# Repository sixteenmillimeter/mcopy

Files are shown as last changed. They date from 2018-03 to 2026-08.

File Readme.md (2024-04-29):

# mcopy

An open platform for controlling small-gauge film optical printers (16mm, Super8, 8mm).

## [Project Home - git.sixteenmillimeter.com/16mm/mcopy](https://git.sixteenmillimeter.com/16mm/mcopy)

* Github Mirror - [github.com/sixteenmillimeter/mcopy](https://github.com/sixteenmillimeter/mcopy)
* Gitlab Mirror - [gitlab.com/16mm/mcopy](https://gitlab.com/16mm/mcopy)

-------
1. <a href="#intro">Introduction</a>
2. <a href="#downloads">Downloads</a>
1. <a href="#usage">Usage</a>
2. <a href="#software">Software</a>
3. <a href="#firmware">Firmware</a>
3. <a href="#hardware">Hardware</a>
4. <a href="#why">Why?</a>

-------

## Introduction 

The `mcopy` project is comprised of software and hardware for optical printers, built with re-purposed broken projectors.

#### Components

* Sequencer desktop app
* Scripting language, called `mscript`, for orchestrating complex sequences
* Arduino firmware for projectors, cameras, lights and existing printers
* 3D models of parts used for modifying projectors and printers
* Schematics for simple Arduino-based electronics
* Filmout feature for digitally transferring video and images to analog film
* Interoperability with the [intval3](https://github.com/sixteenmillimeter/intval3) intervalometer

## Downloads 

### Latest Installers

* [1.6.9](https://github.com/sixteenmillimeter/mcopy/releases/tag/1.6.9) for macOS, Linux (.deb) and Windows (.msi)

### Older Versions
* [1.6.7](https://github.com/sixteenmillimeter/mcopy/releases/tag/1.6.7) for macOS and Linux (.deb)
* [1.6.4](https://github.com/sixteenmillimeter/mcopy/releases/tag/1.6.4) for macOS, Linux (.deb) and Windows (.msi)
* [1.6.2](https://github.com/sixteenmillimeter/mcopy/releases/tag/1.6.2) for macOS
* [1.6.1](https://github.com/sixteenmillimeter/mcopy/releases/tag/1.6.1) for macOS
* [1.5.2](https://github.com/sixteenmillimeter/mcopy/releases/tag/1.5.2) for macOS
* [1.4.9](https://github.com/sixteenmillimeter/mcopy/releases/tag/1.4.9) for macOS and Linux (.deb)
* [1.2.0](https://github.com/sixteenmillimeter/mcopy/releases/tag/1.2.0) for macOS and Linux (.deb)
* [1.0.3](https://github.com/sixteenmillimeter/mcopy/releases/tag/1.0.3) for macOS and Linux (.deb)

For Windows, you can [install from source](https://github.com/sixteenmillimeter/mcopy/tree/master/app#mcopy-desktop-app) for now.

## Usage 

The software requires your hardware to be in place before the mcopy control app is useful.

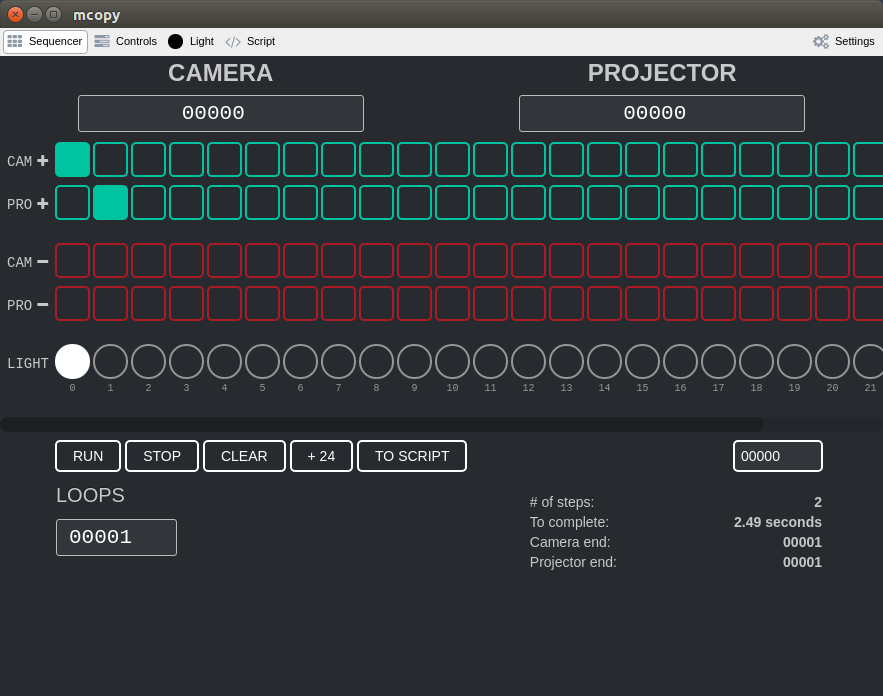
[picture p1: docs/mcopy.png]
mcopy app


## Software 

The mcopy desktop app is an Electron-based project which can be built for Linux, Windows and macOS.
Pre-built packages will be made available for macOS, initially, with the other two target platforms to follow.
To build the desktop app from source, see the [installation and running instructions](https://github.com/sixteenmillimeter/mcopy/tree/master/app#mcopy-desktop-app).
The desktop software also interoperates with two related projects; the Bluetooth + Wifi capable, Raspberry Pi-based [INTVAL3](https://github.com/sixteenmillimeter/intval3) and the Arduino-based [intval2](https://github.com/sixteenmillimeter/intval2).

## Firmware 

This project contains Arduino formware for controlling: 

* a projector
* a camera (see [intval2](https://github.com/sixteenmillimeter/intval2) for more info)
* a light
* a projector + a camera
* a projector + a light
* a camera + a light
* a camera + a projector + a light

Using a simple serial interface, this modular platform can be used to control DIY components, modified existing optical printers or a mixture of components.
The desktop app can connect to multiple serial devices, so your mcopy optical printer can be built from various designs that suit your hardware tastes/needs/available parts.

## Hardware 

All non-electronic hardware for this project is available as plaintext OpenSCAD files and 3D print-able .STL files. 
The hardware component of this project is aimed at modifying broken Bell & Howell projectors into USB serial-controlled projectors to be used in optical printing.

As a secondary capability, this desktop software and firmware package can be used to replace the sequencers for early-model JK optical printers, with some modification.

## Why? 

I'm interested in expanding the viability and access of the 16mm film format and to repurpose thre rising tide of discarded film technology.

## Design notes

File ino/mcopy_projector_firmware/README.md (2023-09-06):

# mcopy projector firmware

The goal of this firmware is to drive a JK-compatible gate
with two (2) NEMA17 stepper motors. Registration will be tracked
by four (4) IR LED emitters and receivers tracking two (2) 
double-stage rotary encoders.

1. log step index
2. calculate volate
3. analogRead() x 3
4. average readings
5. populate array with average at index

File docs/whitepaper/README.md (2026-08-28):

---
fontfamily: tgtermes
title: "mcopy: Modular Optical Tool Platform for Small Gauge Motion Picture Film"
documentclass: article
author:
- name: Matthew McWilliams
  affiliation: sixteenmillimeter.com
  email: hi@mmcwilliams.com
abstract: |
    The mcopy project consists of a modular, open-source platform for building optical tools for small gauge analog motion picture film formats.
    The platform can be used to assemble optical printers, digital transfer units and film recorders for digital images.
    Taking inspiration and guidance from free and open-source hardware and software projects, this approach aims to empower DIY projects that enable artists and artist-run film labs to build their own sytems and design their own practices around their own needs and abilities.
bibliography: sources.bib
csl: citation_style.csl
---

# Introduction

Dennis Couzin explains very plainly, in the opening line of _Notes on Optical Printer Technique_, that "an optical printer is a device for photographing the frames of one film so as to make another film." [@notes-couzin]
Consisting of a camera, a lens, a projector and a light the optical printer is a simple device that provides powerful manipulative analog capabilities to the film artist.
Optical printers allow filmmakers to control time, image and color frame-by-frame and without a digital intermediary.

The mcopy platform was started in 2009 as a one-off retrofit of a broken Bell & Howell projector.
Its initial goal was to create an optical printer with what was available at the time.
Using an Arduino, a toy DC motor, some tin foil and LEDs the first approach was made towards designing this system from otherwise discarded hardware.
Assembling this with a small copy stand and a crudely-controlled Bolex 16mm camera, it performed the function of copying film from the projector to the camera.

# Motivations

A common scenario in the analog filmmaking world is a person or organization in possession of partial or non-working optical printer.
One solution for this, potentially, would be to meticulously replace or repair any missing or non-functional parts.
This proves to be a challenge when the companies that created those parts no longer exist and the documentation for repairing these machines was either never produced or never made public.
It proves even more challenging when the individual elemental components, chips and capacitors, are no longer made in the form factors they were originally produced in and entire boards must be replaced or redesigned to support the specifications they were designed with.

Another complication to any approach to modernizing these machines is that they were produced in small batches with many changes in design between these revisions.
This makes for a very non-standard pool of components to be assembling into a single system.

A remaining solution that presents itself is to "hack" these machines and retrofit them with available techniques.
The counter to that is estabishing a common interface for this platform.
Anything that can be conformed to this new standard can be assimilated and new configurations can be built that were not possible with legacy hardware sequencers.

# Design Philosophy

Tools purpose-built for working with 16mm, Super8 and Regular 8 film are no longer regularly being produced.
There are exceptions, but without a large commercial production demand, manufacturing companies that are theoretically capable of producing the gear required to work with analog film are choosing not to.
This leaves the future of the analog cinema in the hands of its practitioners to steward the continuation and advancement of the art.
By looking to other disciplines, be they arts or sciences, artists who work with film can benefit from the ways that small-scale desktop manufacturing and rapid prototyping have both preserved and augmented other practices.

The RepRap project [@reprap-philosophy]--the "reproducible rapid-prototyper" project that kicked off a wave of open-source 3D printers--correctly does not spend any time focusing on producing alternatives for "cheap and ubiquitous parts like screws and electric motors".
If there is an existing, standard and available part that solves a problem, it saves time and effort inclding it.
Those resources are better spent focusing on the core requirements of the project which, in this case, is to make a cheap and accessible contact printer for artists.

The RepRap project is not a perfect foundation on which to base the entirety of the design of this contact printer, however.
The conclusion drawn by Adrian Bower--an engineer, not a philosopher or historian--that Marxism provides a correct diagnosis of Capital but it's solution is the "all-time worst-idea in human history" [@reprap-philosophy] is both ahistorical and works against the entire purpose of the project.
Contact printing, as a means of film production, benefits more people by shifting from a mode limited to a class of professional film lab operators to a more accessible capability available to artists and artist-run film labs who operate at a sub-industrial scale.

The Arduino project [@arduino-about] created an explosion of capabilities that are now available to hobbyists and educators by making an open and extendable platform of programmable microcontrollers.
Amateurs are offered the ability to control physical electronic hardware with code in a way that was completely inaccessible due to cost and complexity only years prior.
The Arduino improved on the Parallax BASIC Stamp, a closed-source physical computing platform that required special software for the build toolchain, replacing it with an open-source board and an integrated development environment (IDE) for easily programming the board that could run cross-platform. [@arduino-os]
By leveraging the tools themselves--Arduino microcontrollers and software--as well as the projects' own approach to making an open, clear and accessible way to work with electronics the mcopy project can prioritize simplicity and openness over complexity and trade secrets held for profit.

What emerges from the synthesis of newly-accessible machine-computer interfaces and open manufacturing technologies is the possibility to create new tools that serve the needs filmmakers have today.
Every component can be represented by a serial device that connects to a computer and those devices can be sequenced and controlled by a common application.

By pursuing modular design, filmmakers can use the mcopy platform to create multi-purpose tools that change their functionality by changing their configuration.
Making an mcopy-controlled camera module for a film-to-film optical printer saves the time and effort of creating a second mcopy-controlled camera module for a film out digital recording system; they can be the exact same camera with only a different image source.
Similarly the system can be used to swap a film camera for a digital one; the sequencer neither cares nor needs to know whether it's controlling a Bolex or a DSLR.
It just has to operate them in the correct order without overlapping.

Two already emergent advantages over closed-source alternatives are the clear and simple plaintext protocol and the sequencer application that runs cross-platform and ties the system together.

# Serial Protocol

At the heart of the functionality of intermittant-motion film printers like an optical printer is the sequencing of discrete actions.
If the camera and projector both run at the same time, or if one is moving before the other completes an action, motion blur will be introduced to the images.
Frames of film must be resting in place for rephotographing onto film or "scanning" the image digitally in these systems.
So, as a result, the mcopy serial protocol has a simple but effective rule: all physical actions are done one-at-a-time and with request and then confirmation steps.
If the camera is triggered to capture a frame with a byte `c` then the camera device must return that byte `c` to confirm that it is complete and is not moving.

There is a library of action command bytes, an ever-growing list, but at the time of this writing represent a mostly-complete range of functionality for a variety of modular hardware components.

Devices, as of now, are expected to operate on `57600` baud and be excessible over serial by any capable serial client.

# Desktop Application

Due to the simplicity of the protocol, the mcopy desktop application existed in many forms before settling as a cross-platform Electron [@electron] app.

The earliest version was a PHP web application that would compile a sequence into a byte array and then send that over serial to the, then, single Arduino that controlled the physical hardware.
The immediate drawback here is that PHP executes per-request, meaning that the serial connection would have to be re-initalized each time there's a user-interaction or a more complicated logic that would keep a device persisted would need to be put into place.
I had neither the capability or inclination to make this work.

The next version was built in Processing [@processing]--a Java-based application that was built for creative programming--which was much more appropriate for the task but has other drawbacks.
The general-purpose graphical interfaces for Processing, things like text inputs and forms, are not ideal and were difficult to develop with and use.

# Retrofitting Existing Hardware

# New Hardware

Retrofitting existing hardware was always intended as the first step to producing new hardware modules that could eventually completely replace all legacy machine parts.
This approach is sometimes referred to as a "Ship of Theseus pattern" [@wiki-shipoftheseus] and in this application is, simply put: build machines using parts that people and organizations already have until total replacements can be designed.
The practice of retrofitting hardware, in this case, requires the kind of inspection that makes designing replacements possible: detailed measurements, documenting electrical diagrams, and review of sourced components.
Two examples of this pattern being applied and materializing new modular components are the projector and gate designs.

## The Projector

## The Gate

## References

---
refs: |
   ::: {#refs}
   :::
...

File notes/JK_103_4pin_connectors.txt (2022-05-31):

# Ebay

Vintage Cinch Jones 4 Pin Male Connector
https://www.ebay.com/itm/133497068900

VINTAGE CINCH JONES 4 PIN Male Connector Plug
https://www.ebay.com/itm/133633184716

Pair Cinch Jones 4-pin Female Connector Mountable Socket Angle Bracket NOS (QTY)
https://www.ebay.com/itm/224122802125

CINCH P-304-CCT POWER PLUGT 4 PIN
https://www.ebay.com/itm/154258653116

Cinch Jones Beau Molex P-304-cct 38331-5604 Power Connector Plug 4 Pin
https://www.ebay.com/p/20039272321

Beau Cinch S304CCT Jones 4 Pin Socket 38331-8004 Connector Cable Clamp Top
https://www.ebay.com/itm/133503417945

CINCH JONES BEAU MOLEX S-3304-CCT-L 38331-8204 SOCKET 4PIN w/ LATCH FOR YAESU
https://www.ebay.com/itm/400445955283

# NEW

https://www.newark.com/cinch-connectivity-solutions/p-304-cct/plug-socket-connector-plug-4-position/dp/39F282

https://www.alliedelec.com/product/cinch/p304hcct/70152797

brass, stainless steel, brass coated steel

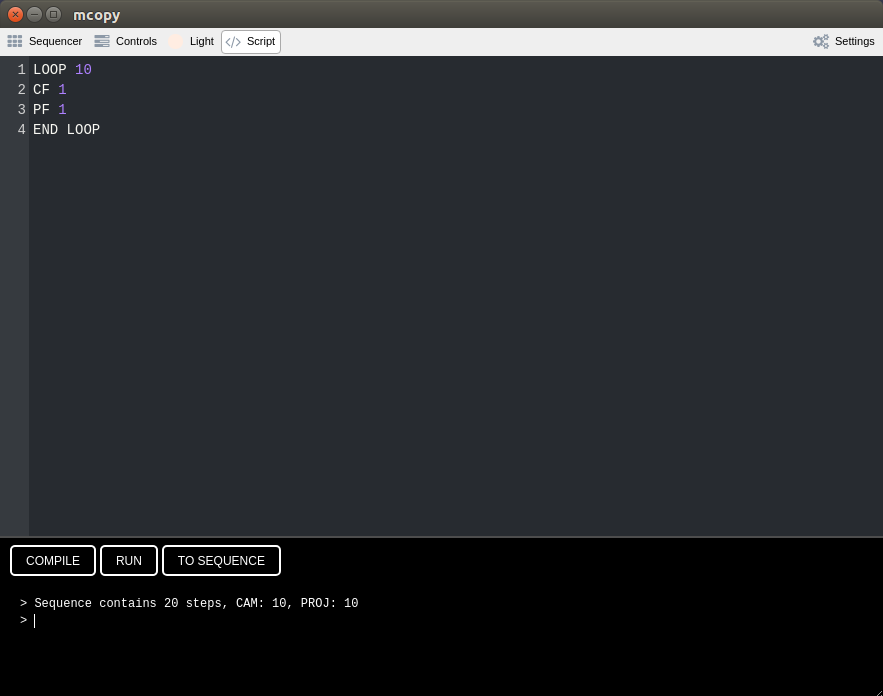
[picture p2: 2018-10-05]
docs/mcopy4.png

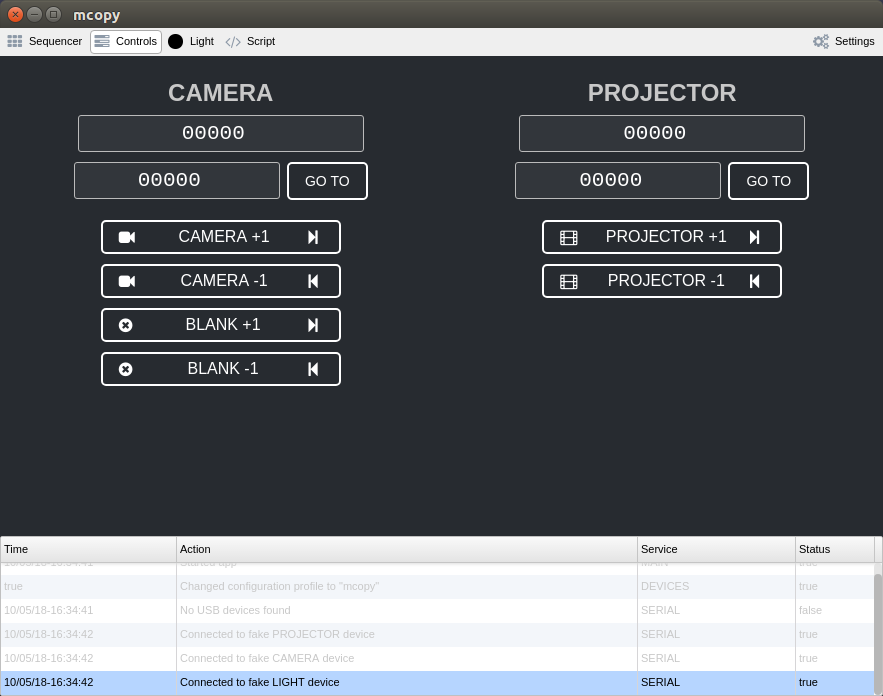
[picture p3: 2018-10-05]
docs/mcopy2.png

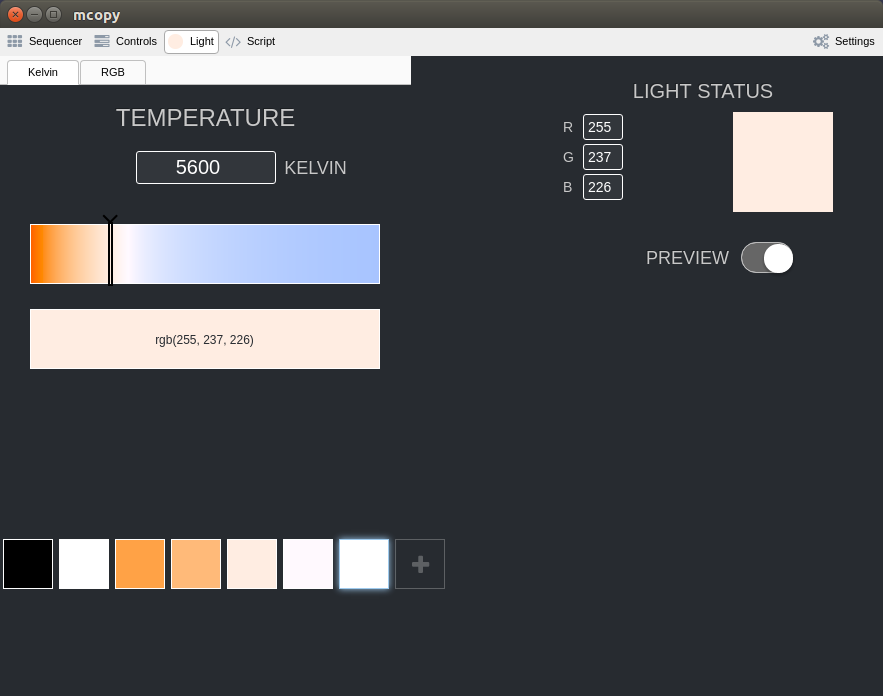
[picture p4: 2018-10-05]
docs/mcopy3.png

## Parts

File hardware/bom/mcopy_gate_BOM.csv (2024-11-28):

module | quantity | part | part_id | description
front_block_pegs | 2 | M2.5 hex cap bolt 10mm | N/A | Fasctens front_block_pegs to front_block
front_block | 4 | M2.5 hex nut | N/A | Attach the film path blocks
front_block | 2 | M5 hex cap bolt 25mm | N/A | Attach the front_block to the body
body | 2 | 608-RS Ball Bearing | 608-RS | Center sprocketed_roller in gate voids and allow for smooth rotation
body | 2 | M3 hex nut | N/A | Attach slide_catch to gate
body | 12 | M2.5 hex nut | ISO 4032 | Attach idle_roller and filter_holder and slide_rail to gate
body | 4 | M2.5 hex cap bolt 10mm | N/A | Attach slide_rail to gate
body | 2 | M2.5 hex cap bolt 25mm | N/A | Attach filter_holder to gate
body | 6 | M2.5 hex cap bolt 16mm | N/A | Attach idle_roller to gate
body | 2 | M5 hex nut | N/A | Attach front_block to gate
body | 2 | M5 hex cap bolt 20mm | N/A | Attach gate to projector
sprocketed_roller_nut_16mm | 2 | M2.5 hex nut | ISO 4032 | Attaches the bolt to the nut
sprocketed_roller_nut_16mm | 2 | M2.5 hex cap bolt 16mm | ISO 4762 | Attaches the nut to the sprocketed roller
back_plate | 1 | M2.5 hex cap bolt 10mm | N/A | Join the front_plate to the back_plate
front_plate | 1 | M2.5 hex nut | ISO 4032 | Join the front_plate to the back_plate

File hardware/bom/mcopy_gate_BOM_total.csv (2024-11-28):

quantity | part | part_id | price
2 | M5 hex nut | N/A | 10
2 | M5 hex cap bolt 25mm | N/A | 54
2 | M5 hex cap bolt 20mm | N/A | 38
2 | M3 hex nut | N/A | 7
19 | M2.5 hex nut | N/A | 120
2 | M2.5 hex cap bolt 25mm | N/A | 12
8 | M2.5 hex cap bolt 16mm | N/A | 112
7 | M2.5 hex cap bolt 10mm | N/A | 98
2 | 608-RS Ball Bearing | 608-RS | 36
46 | TOTAL | N/A | 487

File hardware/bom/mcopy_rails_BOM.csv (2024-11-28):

module | quantity | part | part_id | description
sled | 8 | 608-RS Ball Bearing | 608-RS | To smooth sled moving along rails
sled | 2 | Linear bearing | N/A | For center rails
sled | 2 | T8 Nut | Tr8x2 | For drive screw

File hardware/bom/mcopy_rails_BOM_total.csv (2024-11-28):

quantity | part | part_id | price
2 | T8 Nut | Tr8x2 | 499
2 | Linear bearing | N/A | 200
8 | 608-RS Ball Bearing | 608-RS | 143
12 | TOTAL | N/A | 842

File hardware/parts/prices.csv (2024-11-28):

part | part_id | price | quantity | url
M3 hex nut | N/A | 999 | 300 | https://amzn.to/4hAnwjc
M2.5 hex nut | ISO 4032 | 629 | 100 | https://amzn.to/4i7qxrr
M2.5 hex cap bolt 10mm | N/A | 699 | 50 | https://amzn.to/49froT4
M2.5 hex cap bolt 16mm | N/A | 699 | 50 | https://amzn.to/49cj6v2
M2.5 hex cap bolt 25mm | N/A | 598 | 100 | https://amzn.to/41faYb0
M3 hex cap bolt 6mm | N/A | 726 | 100 | https://amzn.to/3AwiZxo
M3 hex cap bolt 8mm | N/A | 899 | 100 | https://amzn.to/3YEvWNB
M3 hex cap bolt 12mm | N/A | 836 | 100 | https://amzn.to/48CGa5Y
M3 sliding t slot nut | N/A | 599 | 105 | https://amzn.to/48GRrSU
M5 hex cap bolt 20mm | N/A | 949 | 50 | https://amzn.to/4ePHCmW
M5 hex cap bolt 25mm | N/A | 809 | 30 | https://amzn.to/3VgdQAW
M5 hex nut | N/A | 999 | 200 | https://amzn.to/3ZdMNHs
2020 Aluminum extrusion mm | N/A | 7399 | 12200 | https://amzn.to/418OicC
100RPM DC geared motor with encoder | N/A | 1619 | 1 | https://amzn.to/3UF707G
250RPM DC geared motor | JSX40-370 | 1499 | 1 | https://amzn.to/3NWkcRL
ESP32 Dev board | N/A | 1999 | 3 | https://amzn.to/3NXCvGj
L298N Motor driver module | N/A | 1149 | 4 | https://amzn.to/4ellssy
ESP32 GPIO breakout board | N/A | 1199 | 2 | https://amzn.to/3UFjpbO
M4 hex bolt 40mm | N/A | 609 | 10 | https://amzn.to/4ikpYL8
608-RS Ball Bearing | 608-RS | 1779 | 100 | https://amzn.to/4fKxDA7
Linear bearing | LM8UU | 1199 | 12 | https://amzn.to/4i5XsMZ
T8 Nut | Tr8x2 | 499 | 2 | https://amzn.to/3B4m4VW

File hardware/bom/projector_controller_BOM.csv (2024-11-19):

module | quantity | part | part_id | description
electronics_attachment | 2 | M3 hex cap bolt 12mm | N/A | Attach to electronics mount
electronics_mount | 2 | M3 hex nut | N/A | Attach electronics attachment
electronics_mount | 4 | M3 hex cap bolt 8mm | N/A | Attach Arduino Uno

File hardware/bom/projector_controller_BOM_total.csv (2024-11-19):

quantity | part_id | part | price
2 | M3 hex nut | N/A | 6
4 | M3 hex cap bolt 8mm | N/A | 0
2 | M3 hex cap bolt 12mm | N/A | 18
8 | N/A | TOTALS | 24

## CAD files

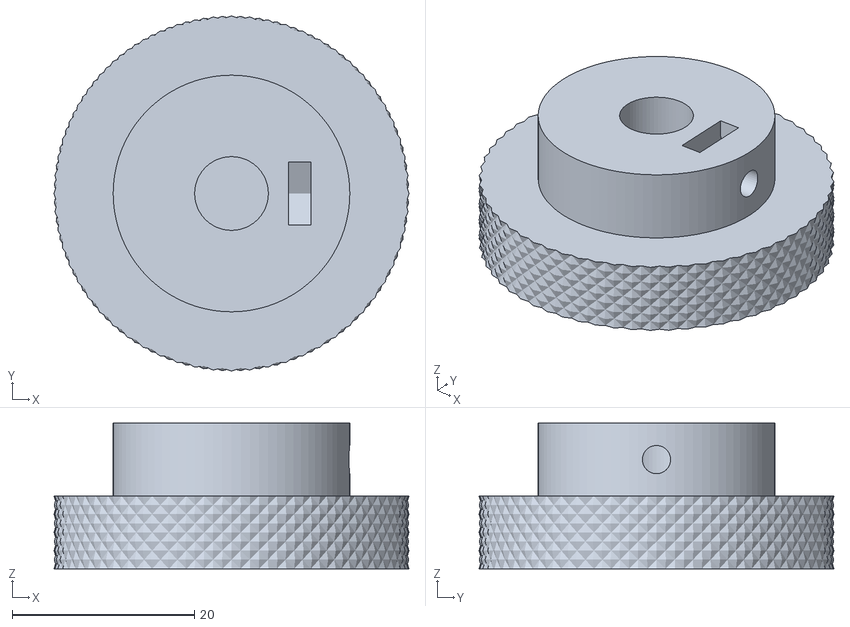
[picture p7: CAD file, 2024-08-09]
stl/mcopy_lens_assembly_threaded_knob.stl
39.0 x 39.0 x 16.0

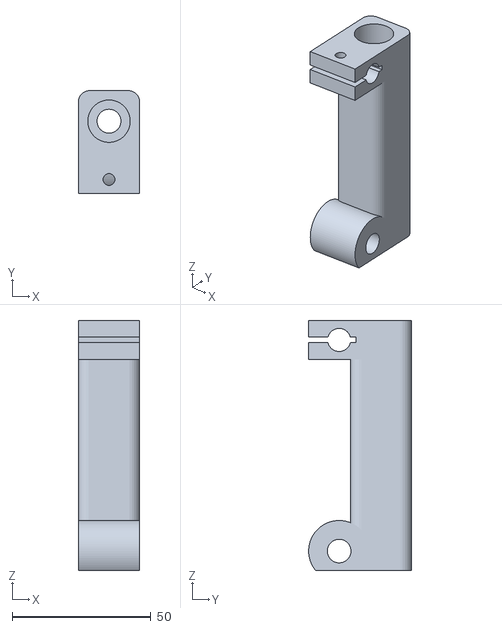
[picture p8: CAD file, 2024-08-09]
stl/mcopy_lens_assembly_linear_z.stl
22.0 x 37.0 x 90.0

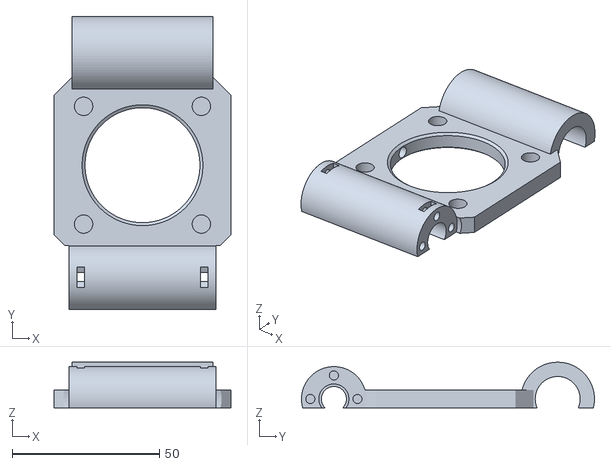
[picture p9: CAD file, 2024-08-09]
stl/mcopy_lens_assembly_bellows_board_magnetic.stl
60.0 x 99.5 x 15.5

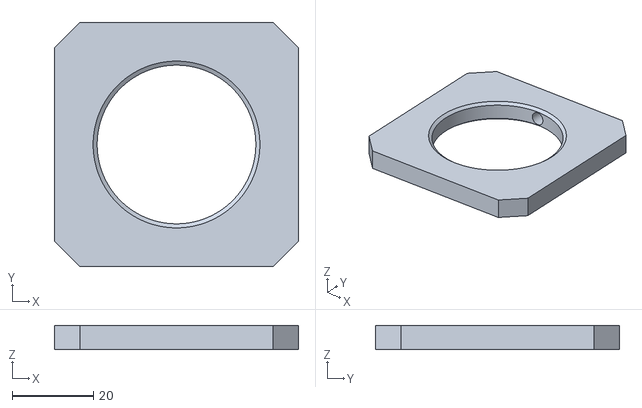
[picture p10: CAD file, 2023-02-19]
stl/jk_lens_assembly_camera_bellows_board.stl
60.0 x 60.0 x 6.00

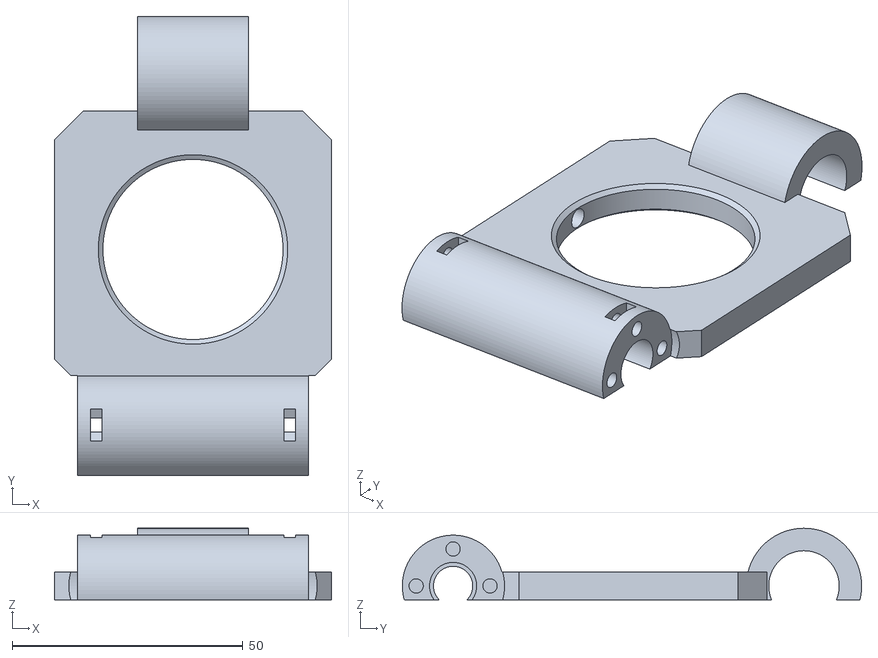
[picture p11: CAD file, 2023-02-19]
stl/jk_lens_assembly_bellows_board.stl
60.0 x 99.5 x 15.5

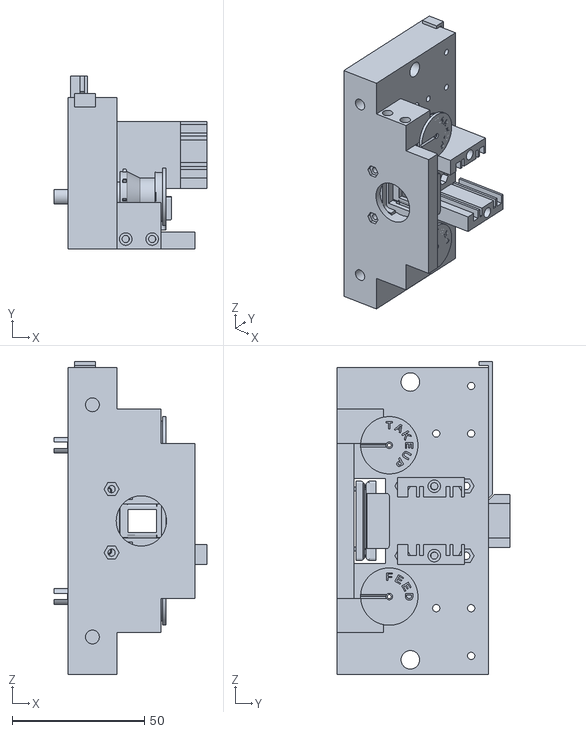
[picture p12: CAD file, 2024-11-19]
debug/mcopy_gate.stl
57.7 x 65.4 x 118.3

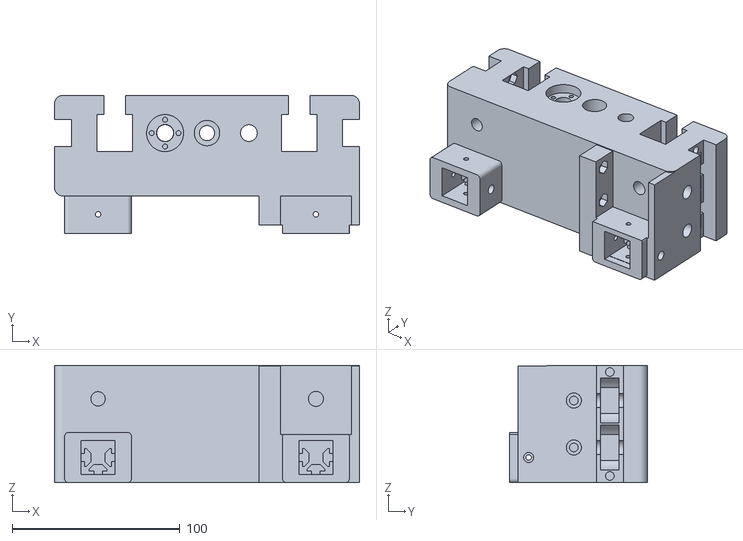
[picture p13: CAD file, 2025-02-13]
stl/mcopy_rails_lens_sled.stl
182.0 x 82.5 x 70.0

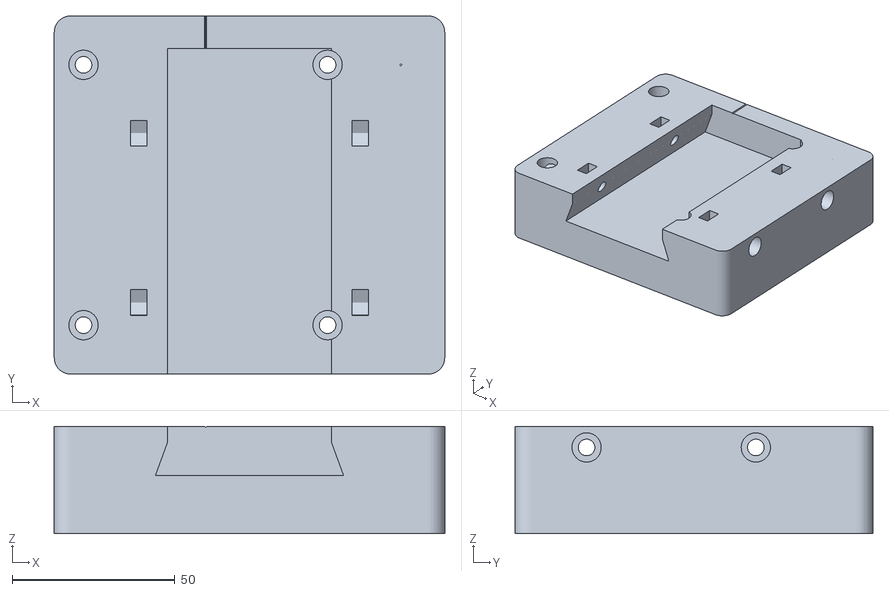
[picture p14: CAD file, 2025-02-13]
stl/mcopy_rails_camera_sled_bolex.stl
120.0 x 110.0 x 33.0

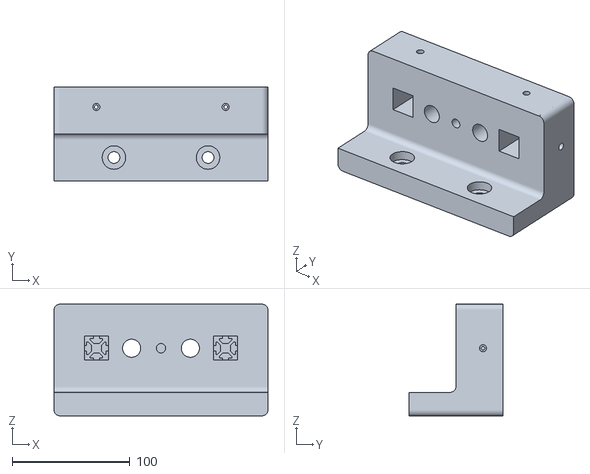
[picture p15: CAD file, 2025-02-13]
stl/mcopy_rails_rail_end_idle.stl
182.0 x 80.0 x 95.0

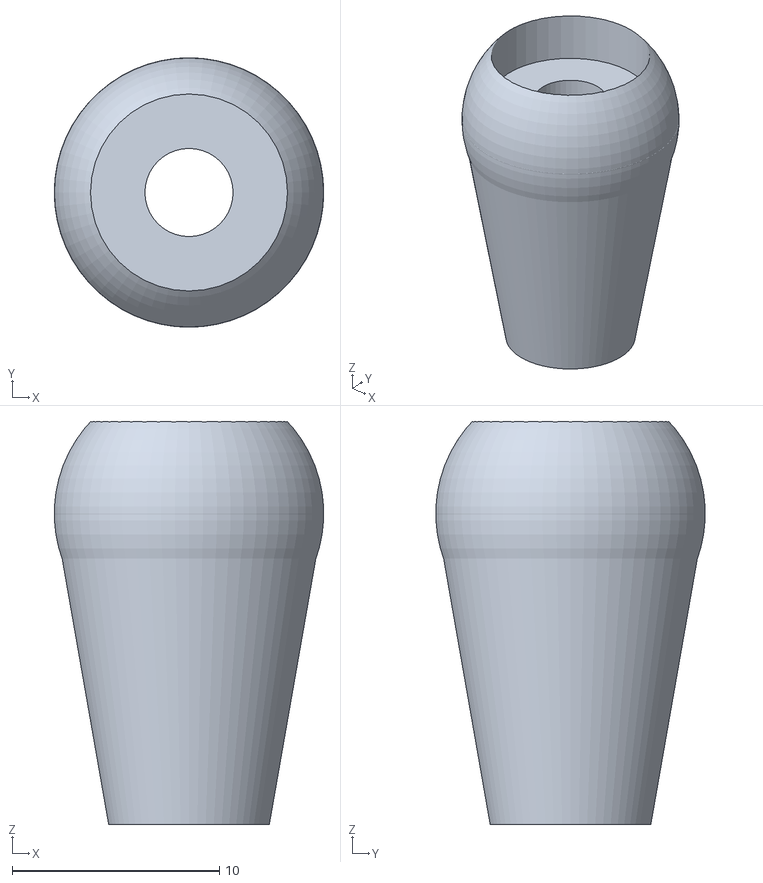
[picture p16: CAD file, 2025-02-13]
stl/mcopy_rails_dial_handle.stl
13.0 x 13.0 x 19.4

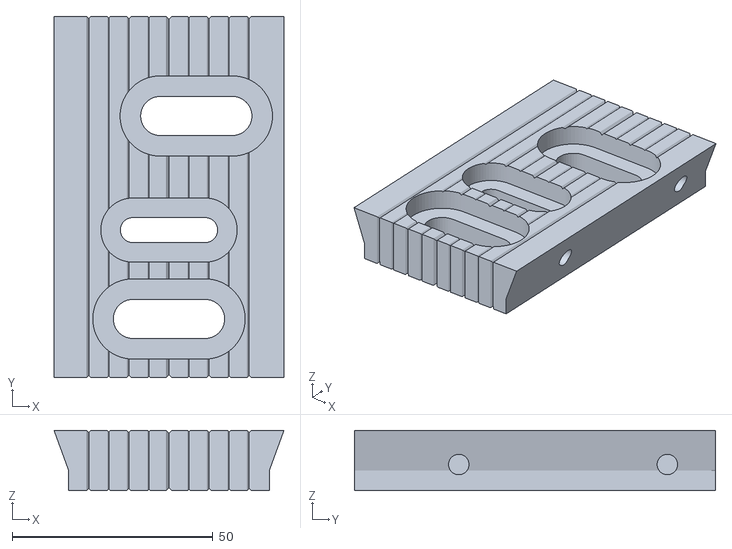
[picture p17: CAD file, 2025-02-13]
stl/mcopy_rails_camera_sled_bolex_plate.stl
57.3 x 90.0 x 15.0

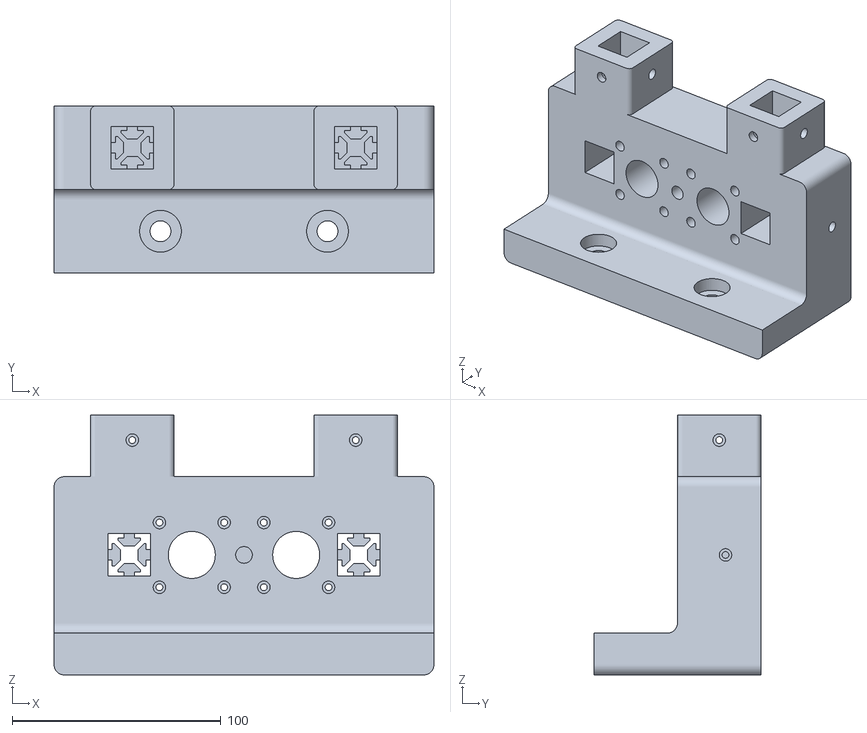
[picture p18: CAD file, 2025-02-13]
stl/mcopy_rails_rail_end.stl
182.0 x 80.0 x 124.5

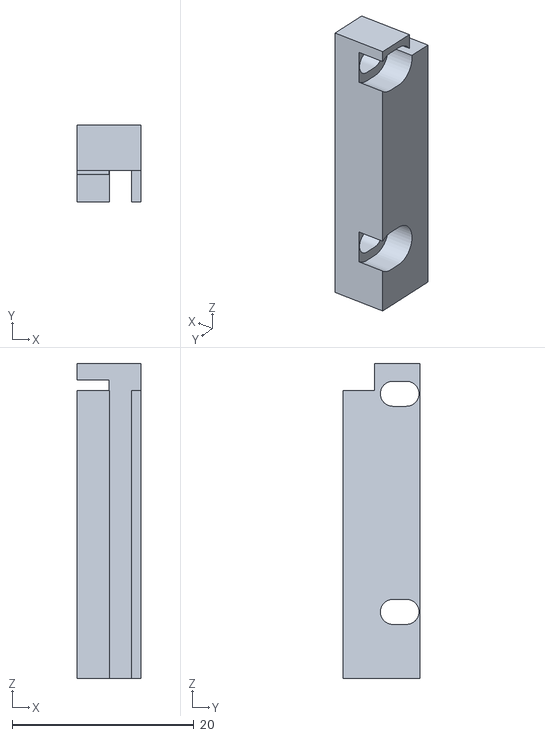
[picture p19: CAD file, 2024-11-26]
stl/mcopy_gate_slide_rail_a.stl
7.00 x 8.50 x 34.7

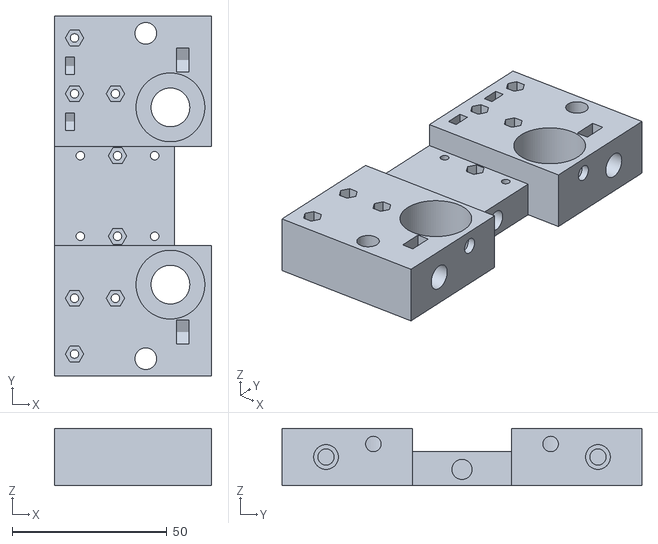
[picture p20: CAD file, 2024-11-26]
stl/mcopy_gate_body_16mm.stl
50.7 x 116.1 x 18.4

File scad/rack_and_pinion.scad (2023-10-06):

// Kopfspiel
spiel = 0.05;
// Hoehe des Zahnkopfes ueber dem Teilkreis
modul=1;
// Laenge der Zahnstange
laenge_stange=50;
// Anzahl der Radzaehne
zahnzahl_ritzel=32;
// Hoehe der Zahnstange bis zur Waelzgeraden
hoehe_stange=4;
// Durchmesser der Mittelbohrung des Stirnrads
bohrung_ritzel=4;
// Breite der Zaehne
breite=8.8;
// Eingriffswinkel, Standardwert = 20 grad gemaess DIN 867. Sollte nicht groesser als 45 grad sein.
eingriffswinkel=20;
// Schraegungswinkel zur Rotationsachse, Standardwert = 0 grad (Geradverzahnung)
schraegungswinkel=20;
// Komponenten zusammengebaut fuer Konstruktion oder auseinander zum 3D-Druck 
zusammen_gebaut=0;
// Loecher zur Material-/Gewichtsersparnis bzw. Oberflaechenvergoesserung erzeugen, wenn Geometrie erlaubt
optimiert = 1;

/* Bibliothek fuer ein Zahstangen-Radpaar fuer Thingiverse Customizer

Enthaelt die Module
zahnstange(modul, laenge, hoehe, breite, eingriffswinkel = 20, schraegungswinkel = 0)
stirnrad(modul, zahnzahl, breite, bohrung, eingriffswinkel = 20, schraegungswinkel = 0, optimiert = true)
zahnstange_und_ritzel (modul, laenge_stange, zahnzahl_ritzel, hoehe_stange, bohrung_ritzel, breite, eingriffswinkel=20, schraegungswinkel=0, zusammen_gebaut=true, optimiert=true)

Autor:      Dr Joerg Janssen
Stand:      6. Januar 2017
Version:    2.0
Lizenz:     Creative Commons - Attribution, Non Commercial, Share Alike

Erlaubte Module nach DIN 780:
0.05 0.06 0.08 0.10 0.12 0.16
0.20 0.25 0.3  0.4  0.5  0.6
0.7  0.8  0.9  1    1.25 1.5
2    2.5  3    4    5    6
8    10   12   16   20   25
32   40   50   60

*/


/* [Hidden] */
pi = 3.14159;
rad = 57.29578;
$fn = 96;

/*  Wandelt Radian in Grad um */
function grad(eingriffswinkel) =  eingriffswinkel*rad;

/*  Wandelt Grad in Radian um */
function radian(eingriffswinkel) = eingriffswinkel/rad;

/*  Wandelt 2D-Polarkoordinaten in kartesische um
    Format: radius, phi; phi = Winkel zur x-Achse auf xy-Ebene */
function pol_zu_kart(polvect) = [
    polvect[0]*cos(polvect[1]),  
    polvect[0]*sin(polvect[1])
];

/*  Kreisevolventen-Funktion:
    Gibt die Polarkoordinaten einer Kreisevolvente aus
    r = Radius des Grundkreises
    rho = Abrollwinkel in Grad */
function ev(r,rho) = [
    r/cos(rho),
    grad(tan(rho)-radian(rho))
];

/*  Wandelt Kugelkoordinaten in kartesische um
    Format: radius, theta, phi; theta = Winkel zu z-Achse, phi = Winkel zur x-Achse auf xy-Ebene */
function kugel_zu_kart(vect) = [
    vect[0]*sin(vect[1])*cos(vect[2]),  
    vect[0]*sin(vect[1])*sin(vect[2]),
    vect[0]*cos(vect[1])
];

/*  prueft, ob eine Zahl gerade ist
    = 1, wenn ja
    = 0, wenn die Zahl nicht gerade ist */
function istgerade(zahl) =
    (zahl == floor(zahl/2)*2) ? 1 : 0;

/*  Kopiert und dreht einen Koerper */
module kopiere(vect, zahl, abstand, winkel){
    for(i = [0:zahl-1]){
        translate(v=vect*abstand*i)
            rotate(a=i*winkel, v = [0,0,1])
                children(0);
    }
}


/*  Zahnstange
    modul = Hoehe des Zahnkopfes ueber der Waelzgeraden
    laenge = Laenge der Zahnstange
    hoehe = Hoehe der Zahnstange bis zur Waelzgeraden
    breite = Breite der Zaehne
    eingriffswinkel = Eingriffswinkel, Standardwert = 20 grad gemaess DIN 867. Sollte nicht groesser als 45 grad sein.
    schraegungswinkel = Schraegungswinkel zur Zahnstangen-Querachse; 0 grad = Geradverzahnung */
module zahnstange(modul, laenge, hoehe, breite, eingriffswinkel = 20, schraegungswinkel = 0) {

    // Dimensions-Berechnungen
    //modul=0.99;// modul*(1-spiel);
    c = modul / 6;                                              // Kopfspiel
    mx = modul/cos(schraegungswinkel);                          // Durch Schraegungswinkel verzerrtes modul in x-Richtung
    a = 2*mx*tan(eingriffswinkel)+c*tan(eingriffswinkel);       // Flankenbreite
    b = pi*mx/2-2*mx*tan(eingriffswinkel);                      // Kopfbreite
    x = breite*tan(schraegungswinkel);                          // Verschiebung der Oberseite in x-Richtung durch Schraegungswinkel
    nz = ceil((laenge+abs(2*x))/(pi*mx));                       // Anzahl der Zaehne
    
    translate([-pi*mx*(floor(nz/2)-1)-a-b/2,-modul,0]){
        intersection(){
            kopiere([1,0,0], nz, pi*mx, 0){
                polyhedron(
                    points=[[0,-c,0], [a,2*modul,0], [a+b,2*modul,0], [2*a+b,-c,0], [pi*mx,-c,0], [pi*mx,modul-hoehe,0], [0,modul-hoehe,0], // Unterseite
                        [0+x,-c,breite], [a+x,2*modul,breite], [a+b+x,2*modul,breite], [2*a+b+x,-c,breite], [pi*mx+x,-c,breite], [pi*mx+x,modul-hoehe,breite], [0+x,modul-hoehe,breite]],   // Oberseite
                    faces=[[6,5,4,3,2,1,0],                     // Unterseite
                        [1,8,7,0],
                        [9,8,1,2],
                        [10,9,2,3],
                        [11,10,3,4],
                        [12,11,4,5],
                        [13,12,5,6],
                        [7,13,6,0],
                        [7,8,9,10,11,12,13],                    // Oberseite
                    ]
                );
            };
            translate([abs(x),-hoehe+modul-0.5,-0.5]){
                cube([laenge,hoehe+modul+1,breite+1]);
            }   
        };
    };  
}

/*  Stirnrad
    modul = Hoehe des Zahnkopfes ueber dem Teilkreis
    zahnzahl = Anzahl der Radzaehne
    breite = Zahnbreite
    bohrung = Durchmesser der Mittelbohrung
    eingriffswinkel = Eingriffswinkel, Standardwert = 20 grad gemaess DIN 867. Sollte nicht groesser als 45 grad sein.
    schraegungswinkel = Schraegungswinkel zur Rotationsachse; 0 grad = Geradverzahnung
    optimiert = Loecher zur Material-/Gewichtsersparnis bzw. Oberflaechenvergoesserung erzeugen, wenn Geometrie erlaubt (= 1, wenn wahr) */
module stirnrad(modul, zahnzahl, breite, bohrung, eingriffswinkel = 20, schraegungswinkel = 0, optimiert = true) {

    // Dimensions-Berechnungen  
    d = modul * zahnzahl;                                           // Teilkreisdurchmesser
    r = d / 2;                                                      // Teilkreisradius
    alpha_stirn = atan(tan(eingriffswinkel)/cos(schraegungswinkel));// Schraegungswinkel im Stirnschnitt
    db = d * cos(alpha_stirn);                                      // Grundkreisdurchmesser
    rb = db / 2;                                                    // Grundkreisradius
    da = (modul <1)? d + modul * 2.2 : d + modul * 2;               // Kopfkreisdurchmesser nach DIN 58400 bzw. DIN 867
    ra = da / 2;                                                    // Kopfkreisradius
    c =  (zahnzahl <3)? 0 : modul/6;                                // Kopfspiel
    df = d - 2 * (modul + c);                                       // Fusskreisdurchmesser
    rf = df / 2;                                                    // Fusskreisradius
    rho_ra = acos(rb/ra);                                           // maximaler Abrollwinkel;
                                                                    // Evolvente beginnt auf Grundkreis und endet an Kopfkreis
    rho_r = acos(rb/r);                                             // Abrollwinkel am Teilkreis;
                                                                    // Evolvente beginnt auf Grundkreis und endet an Kopfkreis
    phi_r = grad(tan(rho_r)-radian(rho_r));                         // Winkel zum Punkt der Evolvente auf Teilkreis
    gamma = rad*breite/(r*tan(90-schraegungswinkel));               // Torsionswinkel fuer Extrusion
    schritt = rho_ra/16;                                            // Evolvente wird in 16 Stuecke geteilt
    tau = 360/zahnzahl;                                             // Teilungswinkel
    
    r_loch = (2*rf - bohrung)/8;                                    // Radius der Loecher fuer Material-/Gewichtsersparnis
    rm = bohrung/2+2*r_loch;                                        // Abstand der Achsen der Loecher von der Hauptachse
    z_loch = floor(2*pi*rm/(3*r_loch));                             // Anzahl der Loecher fuer Material-/Gewichtsersparnis
    
    optimiert = (optimiert && r >= breite*1.5 && d > 2*bohrung);    // ist Optimierung sinnvoll?

    // Zeichnung
    union(){
        rotate([0,0,-phi_r-90*(1-spiel)/zahnzahl]){                     // Zahn auf x-Achse zentrieren;
                                                                        // macht Ausrichtung mit anderen Raedern einfacher
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

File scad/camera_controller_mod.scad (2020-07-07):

PART = "";

MOUNT_DIST = 28 - .5;
MOUNT_ANGLE = 125;
MOUNT_W = 12;
MOUNT_H = 8;
MOUNT_D = 12;

mm_x = [61.5, 21.5, 6, 45.5, 18, 39];
mm_y = [-18, 21, -27.5, -27.5, 7, 39];
mm_r = [110, -15, 0, 0, 0, -70];
mm_l = [13, 9, 0, 0, 0, 8];

xArray = [-3, 57,  55,  -26]; //NO MIDDLE PIN
yArray = [38, 31, -56,  -33]; //NO MIDDLE PIN

outerD = 9;
innerD = 4.5;
height = 17;

panel_2_x = 110;
panel_2_y = 110;

one_to_one_x = 54.5;
one_to_one_y = 12;

bolt_inner = 2.55;

screw_distance = 31;

module rounded_cube (cube_arr = [1, 1, 1], d = 0, center = false) {
	off_x = 0;
	off_y = 0;
	r = d/2;
	union () {
		cube([cube_arr[0] - d, cube_arr[1], cube_arr[2]], center = center);
		cube([cube_arr[0], cube_arr[1] - d, cube_arr[2]], center = center);
		translate ([1 * (cube_arr[0] / 2) - r , 1 * (cube_arr[1] / 2)- r, 0]) cylinder(r = r, h = cube_arr[2], center = center);
		translate ([-1 * (cube_arr[0] / 2) + r, -1 * (cube_arr[1] / 2) + r, 0]) cylinder(r = r, h = cube_arr[2], center = center);
		translate ([1 * (cube_arr[0] / 2) - r, -1 * (cube_arr[1] / 2) + r, 0]) cylinder(r = r, h = cube_arr[2], center = center);
		translate ([-1 * (cube_arr[0] / 2) + r, 1 * (cube_arr[1] / 2)- r, 0]) cylinder(r = r, h = cube_arr[2], center = center);
	}
}

module geared_motor_mount_120 (DECOYS = false) {
    $fn = 160;
	base_d = 35;
	base_inner = 25.2;
	base_thickness = 3;
	hole_d = 7;
	screw_d = 3.2;
    bolt_end = 5.4;
	height = 6;
    screw_distance = 17;
    offset_h = 14;
    
	difference () {
		difference () {
			translate([0, 0, 2.5]) cylinder(r=base_d/2, h=height + 5, center = true); //outer cylinder
            translate([0, 0, base_thickness + 1.5]) cylinder(r=base_inner/2, h=height + 5, center = true); //inner cylinder
		}
		cylinder(r=hole_d/2, h=29, center = true); //center hole
		//screw holes
        translate([0, 0, 0]) {
            translate([0, screw_distance/2, 0]) cylinder(r=screw_d/2, h=29, center = true);
            translate([0, -screw_distance/2, 0]) cylinder(r=screw_d/2, h=29, center = true);
            
            //bolt ends
            translate([0, screw_distance/2, -3]) cylinder(r=bolt_end/2, h=2, center = true);
            translate([0, -screw_distance/2, -3]) cylinder(r=bolt_end/2, h=2, center = true);
        }
        
    }
    
    //mounting arms
    difference ()  {
        union () {
            translate([0, 16, 1]) cube([MOUNT_W, 35 - 12, MOUNT_H], center = true);
            translate([0, 16 + 11.5, 1]) cylinder(r = MOUNT_W / 2, h =  MOUNT_H, center = true);
        }
        translate([0, MOUNT_DIST, 0]) cylinder(r = 4.5 / 2, h = MOUNT_H * 2, center = true);
        cylinder(r=(base_inner + 1) /2, h = 30, center = true);
        translate([0, 16 + 11.5, 7]) cylinder(r = MOUNT_W / 2, h =  MOUNT_H, center = true);
    }
    translate([0, MOUNT_DIST, -(offset_h / 2) - 1]) difference () {
        cylinder(r = MOUNT_D / 2, h = offset_h, center = true);
        cylinder(r = 4.5 / 2, h = offset_h + 1, center = true);
    }
    //mount2
    rotate([0, 0, MOUNT_ANGLE]) {
        difference () {
            union () {
                translate([0, 16, 1]) cube([MOUNT_W, 35 - 12, MOUNT_H], center = true);
                translate([0, 16 + 11.5, 1]) cylinder(r = MOUNT_W / 2, h =  MOUNT_H, center = true);
            }
            translate([0, MOUNT_DIST, 0]) cylinder(r = 4.5 / 2, h = MOUNT_H * 2, center = true);
            cylinder(r=(base_inner + 1) /2, h=30, center = true);
            translate([0, 16 + 11.5, 7]) cylinder(r = MOUNT_W / 2, h =  MOUNT_H, center = true);
        }
        translate([0, MOUNT_DIST, -(offset_h / 2) - 1]) difference () {
            cylinder(r = MOUNT_D / 2, h = offset_h, center = true);
            cylinder(r = 4.5 / 2, h = offset_h + 1, center = true);
        }
    }
        //mount3
    rotate([0, 0, 360 - MOUNT_ANGLE]) {
        difference () {
            union () {
                translate([0, 16 - 8, 1]) cube([MOUNT_W, 21, MOUNT_H], center = true);
                translate([0, 16 - 9 + 11.5, 1]) cylinder(r = MOUNT_W / 2, h =  MOUNT_H, center = true);
            }
            cylinder(r=(base_inner + 1) /2, h=30, center = true);
        }
        difference () {
            translate([0, MOUNT_DIST - 9, -(offset_h / 2) - 1]) {
                cylinder(r = MOUNT_D / 2, h = offset_h, center = true);
            }
            translate([0, 0, -(offset_h / 2) - 1]) cylinder(r=base_d/2, h=offset_h + 1, center = true);
        }
    }
}

module l289N_mount () {
    $fn = 60;
	DISTANCE = 36.5;
	H = 4;
    THICKNESS = 3;
	module stand () {
		difference () {
			cylinder(r1 = 4, r2 = 3, h = H, center = true);
		}
	}
	translate([0, 0, 0]) stand();
	translate([DISTANCE, 0, 0]) stand();
	translate([DISTANCE, DISTANCE, 0]) stand();
	translate([0, DISTANCE, 0]) stand();
    difference () {
        translate([DISTANCE/2, DISTANCE/2, -3]) rounded_cube([DISTANCE + 8, DISTANCE + 8, THICKNESS], 8, center = true); //base
        translate([DISTANCE/2, DISTANCE/2, -3]) rounded_cube([DISTANCE - 5, DISTANCE - 5, THICKNESS + 1], 10, center = true); //base
     }
        translate([0, 0, 2]) cylinder(r = 1.2, h = H, center = true);
        translate([DISTANCE, 0, 2]) cylinder(r = 1.2, h = H, center = true);
        translate([DISTANCE, DISTANCE, 2]) cylinder(r = 1.2, h = H, center = true);
        translate([0, DISTANCE, 2]) cylinder(r = 1.2, h = H, center = true);
    
}



module key_adapter () {
    $fn = 60;
    ID = 3.8;
    D = 4.4;
    H = 10;
    PEG = 7.5;
    difference () {
        union () {
            cylinder(r = D / 2, h = H, center = true);
            translate([0, 3, (H / 2) - .5]) cube([D + 1, 16, 1], center = true);
            translate([0, PEG, (H / 2) - 2]) cylinder(r = 3 / 2, h = 4, center = true);
        }
        translate([0, 0, 2]) difference () {
            cylinder(r = ID / 2, h = H, center = true);
            translate([ID / 2 + 1.5, 0, 0]) cube([ID, ID, H], center = true);
        }
    }
}

module key () {
    tighten = 0.25;
	difference () {
		cylinder(r = 6.7 / 2, h = 5, center = true);
		cylinder(r = (4.76 -+ tighten) / 2, h = 5, center = true);
	}
	translate ([0, 0, -7.5]) {
		cylinder(r = 6.7 / 2, h = 10, center = true);
	}
}
module keyHole () {
	translate ([0, 0, 1.75]) {
		cube([10, 2, 3.5], center = true);
	}
}
module key_end (rotArr = [0, 0, 0], transArr = [0, 0, 0], ALT = false) {
	translate(transArr) {
		rotate (rotArr) {
			difference () {
				key();
				keyHole();
                if (ALT) {
                    translate([-2.5, 0, 1.75]) cube([5, 3, 3.5], center= true);
                }
			}
		}
	}
}

module hobbled_rod_120 (h = 10) {
    d = 4.25;
    diff = 3.53;
    difference () {
        
        cylinder(r = d/2, h = h, center = true, $fn = 60);
        translate([d/2 + ((d/2) - (d - diff)), 0, 0]) cube([d, d, h + 1], center = true);
    }
}

module motor_key_120 (half = false, DECOYS = false, sides = 1, ALT = false) {
    innerD = 7.85;
	outer_d = 25;//27.5 + 2;
	notch_d = 10;
	height = 9;
	diff = 14 + 2.5 + 2;
    $fn = 60;
	difference () {
		union () {
			translate([one_to_one_x, one_to_one_y, 14.5]) cylinder(r1 = 14 / 2, r2 = 14/2 + 4, h = 5, center = true);// padding against bearing
			translate([one_to_one_x, one_to_one_y, diff - 2]) cylinder(r=outer_d/2, h= height -2, center= true, $fn=200); //large cylinder
			translate([one_to_one_x, one_to_one_y, 6 - 2]) cylinder(r=innerD/2, h= 14, center= true);
            translate([one_to_one_x, one_to_one_y, 8 ]) cylinder(r=9/2, h= 10, center= true);
            key_end([0, 180, -35], [one_to_one_x, one_to_one_y, -3.5 - 3], ALT = ALT); // longer for laser cut board
		}
        //1 notch
		translate([one_to_one_x, one_to_one_y, diff]) {
			translate ([-outer_d/2 - 3.5, 0, 0]) cylinder(r=notch_d/2, h= height + 4, center= true); //notch
		}
        
		//slot for hobbled(?) end
        translate([one_to_one_x, one_to_one_y, 17 + 0]) {
            translate([0, 0, 2.5]) hobbled_rod_120(12);
            //translate([6.42 - .2, 0, 4.3 - 5.5]) rotate([0, 90, 0]) motor_set_screw_120_alt();
            //translate([14, 0, 4.3 - 5.5]) rotate([0, 90, 0]) cylinder(r2 = 6 / 2, r1 = 5.8 / 2, h = 6, center = true); //extension
        
        }
	}
}

module motor_set_screw_120 () {
    cube([10.19, 2.95, 2.95], center = true);
    translate([(10.19 / 2) - (2.56 / 2), 0, 0]) cube([2.56, 5.8, 5.8], center = true);    
}

module motor_set_screw_120_alt () {
    $fn = 60;
    cylinder(r = 2.95 / 2, h = 10.19, center= true);
    translate([0, 0, (10.19 / 2) - (2.56 / 2)]) cylinder(r = 5.8 / 2, h = 2.56, center = true);
}
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

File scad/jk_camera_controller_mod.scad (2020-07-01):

module rounded_cube (c, d) {
    r = d / 2;
    scaled = [c[0] - d, c[1] - d, c[2] - d];
    minkowski() {
        sphere(r = r);
        cube(scaled, center = true);
    }
}

module case () {
    $fn = 100;
    
    X = 75+1;
    Y = 65+1;
    Z = 35+1;
    
    MOUNT_X = 44.5;
    MOUNT_Y = 33.5;
    
    MOUNT_Z1 = 4.5;
    MOUNT_Z2 = 3;
    
    MOUNT_D1 = 5;
    MOUNT_D2 = 2.5;
    
    MOUNT_OFFSET_X = 11;
    MOUNT_OFFSET_Y = 2;
    MOUNT_OFFSET_Z = 13.5;
    
    PLUG_D1 = 15.75;
    PLUG_D2 = 20;
    PLUG_Z = -2;
    PLUG_OFFSET_X = -23;
    
    M5 = 5.75;
    
    difference () {
        rounded_cube([X, Y, Z], d = 8);
        //inner void
        rounded_cube([X - 7, Y - 7, Z - 7], d = 5);
        //top
        translate([0, 0, -Z + 4]) cube([X + 1, Y + 1, Z], center = true);
        //
        translate([PLUG_OFFSET_X, 0, 10]) cylinder(r = PLUG_D1 / 2, h = 20, center = true);
        translate([PLUG_OFFSET_X, 0, 5 - PLUG_Z]) cylinder(r = PLUG_D2 / 2, h = 20, center = true);
        
        //m5
        translate([PLUG_OFFSET_X + 6, 20, 10]) cylinder(r = M5 / 2, h = 50, center = true);
        translate([PLUG_OFFSET_X + 6, -20, 10]) cylinder(r = M5 / 2, h = 50, center = true);
    }
    translate([MOUNT_OFFSET_X, MOUNT_OFFSET_Y, 0]) rotate([0, 0, 90]) {
        translate ([(MOUNT_X / 2), MOUNT_Y / 2, MOUNT_OFFSET_Z]) {
            cylinder(r = MOUNT_D1 / 2, h = MOUNT_Z1, center = true);
            translate([0, 0, -(MOUNT_Z1 / 2) - (MOUNT_Z2 / 2)]) cylinder(r = MOUNT_D2 / 2, h = MOUNT_Z2, center = true);
        }
        translate ([-(MOUNT_X / 2), MOUNT_Y / 2, MOUNT_OFFSET_Z]) {
            cylinder(r = MOUNT_D1 / 2, h = MOUNT_Z1, center = true);
            translate([0, 0, -(MOUNT_Z1 / 2) - (MOUNT_Z2 / 2)]) cylinder(r = MOUNT_D2 / 2, h = MOUNT_Z2, center = true);
        }
        translate ([(MOUNT_X / 2), -MOUNT_Y / 2, MOUNT_OFFSET_Z]) {
            cylinder(r = MOUNT_D1 / 2, h = MOUNT_Z1, center = true);
            translate([0, 0, -(MOUNT_Z1 / 2) - (MOUNT_Z2 / 2)]) cylinder(r = MOUNT_D2 / 2, h = MOUNT_Z2, center = true);
        }
        translate ([-(MOUNT_X / 2), -MOUNT_Y / 2, MOUNT_OFFSET_Z]) {
            cylinder(r = MOUNT_D1 / 2, h = MOUNT_Z1, center = true);
            translate([0, 0, -(MOUNT_Z1 / 2) - (MOUNT_Z2 / 2)]) cylinder(r = MOUNT_D2 / 2, h = MOUNT_Z2, center = true);
        }
    }
    //m5
    translate([PLUG_OFFSET_X + 6, 20, 2]) difference () {
        union () {
            cylinder(r = 9 / 2, h = Z - 5, center = true);
            translate([0, 0, Z / 2 - 6]) cylinder(r = 12 / 2, h = 6, center = true);
        }
        cylinder(r = M5 / 2, h = 50, center = true);
    }
    translate([PLUG_OFFSET_X + 6, -20, 2]) difference () {
        union () {
            cylinder(r = 9 / 2, h = Z - 5, center = true);
            translate([0, 0, Z / 2 - 6]) cylinder(r = 12 / 2, h = 6, center = true);
        }
        cylinder(r = M5 / 2, h = 50, center = true);
    }
    translate([-(X / 2) + 4, Y / 5 , (Z / 2) - 5]) {
            rotate([90, 0, 0]) cylinder(r = 3, h = 10, center = true);
    }
    translate([-(X / 2) + 4, -Y / 5 , (Z / 2) - 4]) {
            rotate([90, 0, 0]) cylinder(r = 3, h = 10, center = true);
    }
    /*translate ([(X / 2) + 5, 0, -9.5]) difference () {
        rounded_cube([15, 15, 5], d = 2);
        translate([0, 0, -4]) cube([15, 15, 5], center = true);
        translate([2, 0, 0]) cylinder(r = M5 / 2, h = 10, center = true);
    }
    translate ([-(X / 2) - 5, 0, -9.5]) difference () {
        rounded_cube([15, 15, 5], d = 2);
        translate([0, 0, -4]) cube([15, 15, 5], center = true);
        translate([-2, 0, 0]) cylinder(r = M5 / 2, h = 10, center = true);
    }*/
}

//intersection () {
difference () {
    case();
    //translate([-23, 0, 0]) cube([100, 100, 100], center = true); 
}
//    translate([-14, 0, 12]) cube([10, 40, 10], center = true);
//}

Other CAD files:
stl/mcopy_lens_assembly_threaded_z.stl
stl/mcopy_gate_front_block_16mm.stl
stl/mcopy_gate_sprocketed_roller_takeup_16mm.stl
stl/mcopy_gate_idle_roller_16mm.stl
scad/mitchell_camera_motor.scad
scad/2020_profile.scad
scad/Canon_EF_body_cap.scad
scad/K-103_electronics.scad
scad/anyeye_revere.scad
scad/arduino.scad
scad/arduino_nano_eos_case.scad
scad/arduino_sainsmart8_case.scad
scad/arduino_sainsmart8_sainsmart4_case.scad
scad/arri_s.scad
scad/arri_s_mount.scad
scad/bellows.scad
scad/bolex.scad
scad/box_laser.scad
scad/cable_protector.scad
scad/canon_ef_bellows_adapter.scad
scad/canon_ef_m_bellows_adapter.scad
scad/canon_mount.scad
scad/canon_rf_ACME_bellows_adapter.scad
scad/canon_rf_ACME_camera_mount.scad
scad/capper.scad
scad/carriage.scad
scad/connectors.scad
scad/cpc_connectors.scad
scad/daylight_spool_mount.scad
scad/dc_plug_cheat.scad
scad/ef_m_mount_v3.scad
scad/esp32_case.scad
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

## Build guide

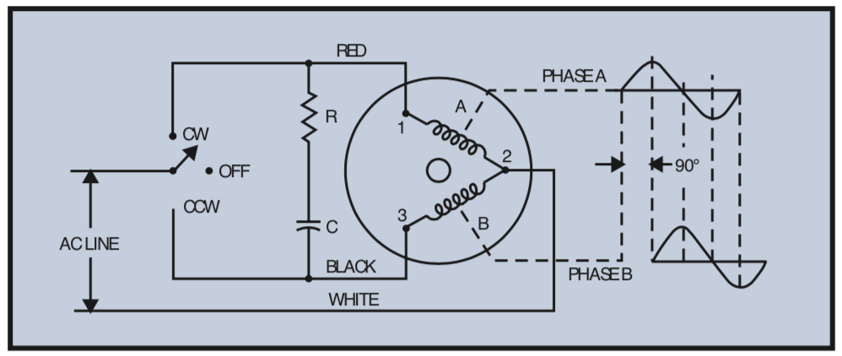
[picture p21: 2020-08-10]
notes/Wiring_for_2_phase_motors.png

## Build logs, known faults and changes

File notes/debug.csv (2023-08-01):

time | state
3000 | 0
3000 | 0
3000 | 0
3000 | 0
3001 | 0
3001 | 0
3001 | 0
3002 | 0
3002 | 0
3002 | 0
3002 | 0
3004 | 0
3005 | 0
3006 | 0
3007 | 0
3009 | 0
3010 | 0
3011 | 0
3013 | 0
3014 | 0
3015 | 0
3017 | 0
3018 | 0
3019 | 0
3021 | 0
3022 | 0
3023 | 0
3025 | 0
3026 | 0
3027 | 0
3030 | 0
3031 | 0
3032 | 0
3034 | 0
3035 | 0
3036 | 0
3038 | 0
3039 | 0
3040 | 0
3042 | 0
3043 | 0
3044 | 0
3046 | 0
3047 | 0
3048 | 0
3050 | 0
3051 | 0
3052 | 0
3054 | 0
3055 | 0
3056 | 0
3058 | 0
3059 | 0
3060 | 0
3062 | 0
3063 | 0
3064 | 0
3066 | 0
3067 | 0
3068 | 0
3070 | 0
3072 | 0
3073 | 0
3075 | 0
3076 | 0
3077 | 0
3079 | 0
3080 | 0
3081 | 0
3083 | 0
3084 | 0
3085 | 0
3087 | 0
3088 | 0
3089 | 0
3091 | 0
3092 | 0
3093 | 0
3094 | 0
3096 | 0
3097 | 0
3098 | 0
3100 | 0
3101 | 0
3102 | 0
3104 | 0
3105 | 0
3106 | 0
3108 | 0
3109 | 0
3110 | 0
3112 | 0
3113 | 0
3115 | 0
3117 | 0
3118 | 0
3119 | 0
3121 | 0
3122 | 0
3123 | 0
3125 | 0
3126 | 0
3127 | 0
3129 | 0
3130 | 0
3131 | 0
3133 | 0
3134 | 0
3135 | 0
3137 | 0
3138 | 0
3139 | 0
3141 | 0
3142 | 0
3143 | 0
3145 | 0
3146 | 0
3147 | 0
3149 | 0
3150 | 0
3151 | 0
3153 | 0
3154 | 0
3155 | 0
3158 | 0
3159 | 0
3160 | 0
3162 | 0
3163 | 0
3164 | 0
3166 | 0
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

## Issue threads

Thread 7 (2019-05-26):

The "From Sequence" feature inserts bad lines

sixteenmillimeter, 2019-05-26:
Namely, "undefined". This is probably a problem in grid.js

sixteenmillimeter, 2019-05-28:
This is resolved in the 1.4.9 release.

Closed 2019-05-28.

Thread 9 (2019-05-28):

GOTO button on projector 2 does not work.

sixteenmillimeter, 2019-05-28:
Not wired up to anything. Doesn't trigger an action.

Closed 2019-05-28.

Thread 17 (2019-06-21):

Frame counting method takes a long time on large videos

sixteenmillimeter, 2019-06-21:
Improve the frame counting feature for filmout so that it determines frame count using better than

```
ffprobe -v error -count_frames -select_streams v:0 -show_entries stream=nb_read_frames -of default=nokey=1:noprint_wrappers=1 "${video}"
```

sixteenmillimeter, 2019-07-03:
This has been resolved with commit f239f862e8b44f925d5ec8c7ab943d622c73ff56. For every type of supported video format or container *except* .mkv (Matroska) there is a new ffprobe command which runs in a fraction of the time. For .mkv files, the old command is used.

Closed 2019-07-03.

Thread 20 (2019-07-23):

Revive server feature

sixteenmillimeter, 2019-07-23:
Enable the remote server feature so that a mobile phone or seperate computer can be used to manually control the optical printer. This can potentially lead to a "headless" mode, but for right now the server should just give the user a mobile interface with a few buttons for advancing and rewinding the camera and the projector.

Closed 2023-03-21.

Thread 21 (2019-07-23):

Camera and projector counters on Sequencer page don't update counts`

sixteenmillimeter, 2019-07-23:
The counters display the state of the camera and projectors, but right now updating the count on the sequencer page does not update the count in the app. It works on the Controls page.

sixteenmillimeter, 2019-07-25:
Bug was only occurring with the camera counter. Resolved in commit f0804fe23bb65e4230cfd00f27ab1474c36856dc

Closed 2019-07-25.

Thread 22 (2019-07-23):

Camera and projector counters remained highlighted after updating

sixteenmillimeter, 2019-07-23:
This occurs on the Controls page. Haven't seen it on the Sequencer page. When the value of the counter for the projector or camera is updated, the counter remains in the highlighted yellow "haven't been changed yet" state. They should return to the default color scheme when the count is updated and correctly displayed.

Closed 2020-01-20.

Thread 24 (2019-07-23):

Address security concerns in modules

sixteenmillimeter, 2019-07-23:
Update node modules to get github to stop yelling at me. This isn't essential until the server feature is re-added, but this really shouldn't be put on an outward facing network. Like, c'mon, people.

Twitch plays optical printer would be pretty cool, though.

Closed 2019-12-17.

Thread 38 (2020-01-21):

Wait until image is fully painted in window before advancing a filmout frame

sixteenmillimeter, 2020-01-21:
Wait for image to be loaded and painted in browser window to signal back to sequencer that the frame is "done". Logging as a bug because of potential issues with filmout feature currently.

Alternate idea: explore using MLT on mac/linux.

Closed 2020-02-21.

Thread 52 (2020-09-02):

Add serial command/protocol for throwing an error from the hardware

sixteenmillimeter, 2020-09-02:
Need to be able to pass an error from mcopy firmware to the app over serial in a situation where synchronous behavior is not occurring. If a frame takes too long or is abnormally short, the firmware should be able to send a character or formatted string to the app so that the user is alerted to the issue and the sequence pauses/stops/cancels. This will prevent sequences from running through multiple errors and will give users a chance to fix physical problems with their hardware.

sixteenmillimeter, 2020-09-29:
Decided on reserving the capital 'E' character as a catch-all error signal from the firmware. If the arduino module catches a stray 'E' it will signal the main process and the renderer process to *pause* (not stop) a sequence. Need to test this on real firmware, but have outlined this in an upcoming commit.

Closed 2023-03-21.

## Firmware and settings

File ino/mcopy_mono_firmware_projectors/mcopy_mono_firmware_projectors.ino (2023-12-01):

/**
 * This is a specialized version of the mcopy firmware for
 * controlling the projectors of the optical printer 
 * at MONO NO AWARE. This uses a Sainsmart 8 Solid State Relay 
 * board wired into the directional switches of a JK104-R projector 
 * controller box, a secondary projector controller box and it 
 * runs on an Arduino Mega 1280 compatible board.
 * 
 * Pins - 8CH Sainsmart Solid State Relay Board
 * 12 - CH1 - BWD PROJ 1
 * 11 - CH2 - FWD PROJ 1 (bridged to CH1)
 * 10 - CH3 - BWD PROJ 1
 * 09 - CH4 - FWD PROJ 1  (bridged to CH3)
 * 08 - CH5 - BWD PROJ 1
 *  - controls the directional relays of the primary projector.
 * 07 - CH8 - 4 pronged trigger cable
 *  - triggers the primary projectory
 * 
 * Pins - 4CH Sainsmart Solid State Relay Board
 * 06 - CH1 - FWD PROJ2
 * 05 - CH2 - FWD PROJ2
 */

boolean debug_state = false;

const int proj_bwd_pin_1 = 12;
const int proj_fwd_pin_1 = 11;
const int proj_bwd_pin_2 = 10;
const int proj_fwd_pin_2 = 9;
const int proj_bwd_pin_3 = 8;
const int proj_pin = 7;

const int proj_second_fwd_pin = 6;
const int proj_second_bwd_pin = 5;
const int proj_second_pin = 4;

const int proj_momentary = 90;
const int proj_time = 950; //secondary projector speed
const int proj_delay = 42;

const int proj_second_momentary = 60;
const int proj_second_time = 950; //adjust
const int proj_second_delay = 42; //use same

boolean proj_dir = true; 
boolean proj_running = false;

boolean proj_second_dir = true;
boolean proj_second_running = false;

const char cmd_projector = 'p';
const char cmd_proj_forward = 'g';
const char cmd_proj_backward = 'h';

const char cmd_proj_second_forward = 'u';
const char cmd_proj_second_backward = 'v';
const char cmd_projector_second = 'w';

const char cmd_projectors = 'x';

const char cmd_debug = 'd';
const char cmd_connect = 'i';
volatile char cmd_char = 'z';
const char cmd_mcopy_identifier = 'm';
const char cmd_proj_identifier = 'x'; //dual projector identifier
//const char cmd_proj_identifier = 'j'; //single projector identifier

const int serialDelay = 5;

void setup() {
  Serial.begin(57600);
  Serial.flush();
  Serial.setTimeout(serialDelay);

  Pins_init();
}

void loop() {
  if (Serial.available()) {
    /* read the most recent byte */
    cmd_char = (char)Serial.read();
  }
  if (cmd_char != 'z') {
    cmd(cmd_char);
    cmd_char = 'z';
  }
}

void cmd (char val) {
  if (val == cmd_debug) {
    debug();
  } else if (val == cmd_connect) {
    connect();
  } else if (val == cmd_mcopy_identifier) {
    identify();
  } else if (val == cmd_projector) {
    projector();
  } else if (val == cmd_proj_forward) {
    proj_direction(true);
  } else if (val == cmd_proj_backward) {
    proj_direction(false);
  } else if (val == cmd_proj_second_forward) {
    proj_second_direction(true);
  } else if (val == cmd_proj_second_backward) {
    proj_second_direction(false);
  } else if (val == cmd_projector_second) {
    projector_second();
  } else if (val == cmd_projectors) {
    projectors();
  }
}

void debug () {
  debug_state = true;
  Serial.println(cmd_debug);
  log("debugging enabled");
}

void connect () {
  Serial.println(cmd_connect);
  log("connect()");
}

void identify () {
  Serial.println(cmd_proj_identifier);
  log("identify()");  
}

void projector () {
  if (!proj_running) {
    proj_running = true;
    digitalWrite(proj_pin, HIGH);
    
    delay(proj_momentary);
    digitalWrite(proj_pin, LOW);
  
    delay(proj_time - proj_momentary + proj_delay);
    
    Serial.println(cmd_projector);
    log("projector()");
    proj_running = false;
    
  }
}

void projector_second () {
  if (!proj_second_running) {
    proj_second_running = true;
    digitalWrite(proj_second_pin, HIGH);
    
    delay(proj_second_momentary);
    digitalWrite(proj_second_pin, LOW);
  
    delay(proj_second_time - proj_second_momentary + proj_second_delay);
    
    Serial.println(cmd_projector_second);
    log("projector_second()");
    proj_second_running = false;
  }
}

void projectors () {
  int proj_time_highest = proj_time;
  if (!proj_running && !proj_second_running) {
    if (proj_second_time > proj_time) {
      proj_time_highest =  proj_second_time;
    }
    proj_running = true;  
    proj_second_running = true;
    
    digitalWrite(proj_pin, HIGH);
    digitalWrite(proj_second_pin, HIGH);
    delay(proj_momentary); //highest? they are the same
    digitalWrite(proj_pin, LOW);
    digitalWrite(proj_second_pin, LOW);
  
    delay(proj_time_highest - proj_momentary + proj_delay);
    
    Serial.println(cmd_projectors); //cmd_projectors
    log("projectors()");
    proj_running = false;
    proj_second_running = false;
  }
}

void proj_direction (boolean state) {
  proj_dir = state;
  digitalWrite(proj_fwd_pin_1, LOW);
  digitalWrite(proj_fwd_pin_2, LOW);

  digitalWrite(proj_bwd_pin_1, LOW);
  digitalWrite(proj_bwd_pin_2, LOW);
  digitalWrite(proj_bwd_pin_3, LOW);
  if (state) {
    digitalWrite(proj_fwd_pin_1, HIGH);
    digitalWrite(proj_fwd_pin_2, HIGH);
    
    Serial.println(cmd_proj_forward);
    log("proj_direction -> true");
  } else {
    digitalWrite(proj_bwd_pin_1, HIGH);
    digitalWrite(proj_bwd_pin_2, HIGH);
    digitalWrite(proj_bwd_pin_3, HIGH);
    
    Serial.println(cmd_proj_backward);
    log("proj_direction -> false");
  }
  //delay(50); //delay after direction change to account for slippage of the belt
}

void proj_second_direction (boolean state) {
  proj_second_dir = state;
  digitalWrite(proj_second_fwd_pin, LOW);
  digitalWrite(proj_second_bwd_pin, LOW);
  if (state) {
    digitalWrite(proj_second_fwd_pin, HIGH);
    Serial.println(cmd_proj_second_forward);
    log("proj_second_direction -> true");
  } else {
    digitalWrite(proj_second_bwd_pin, HIGH);
    Serial.println(cmd_proj_second_backward);
    log("proj_second_direction -> false");
  }
}

void Pins_init () {
  //Declare primary projector pins
  pinMode(proj_fwd_pin_1, OUTPUT);
  pinMode(proj_bwd_pin_1, OUTPUT);
  pinMode(proj_fwd_pin_2, OUTPUT);
  pinMode(proj_bwd_pin_2, OUTPUT);
  pinMode(proj_bwd_pin_3, OUTPUT);
  pinMode(proj_pin, OUTPUT);

  //declare secondary projector pins
  pinMode(proj_second_fwd_pin, OUTPUT);
  pinMode(proj_second_bwd_pin, OUTPUT);
  pinMode(proj_second_pin, OUTPUT);

  //Set primary projector to forward
  digitalWrite(proj_pin, LOW);
  digitalWrite(proj_fwd_pin_1, HIGH);
  digitalWrite(proj_fwd_pin_2, HIGH);
  digitalWrite(proj_bwd_pin_1, LOW);
  digitalWrite(proj_bwd_pin_2, LOW);
  digitalWrite(proj_bwd_pin_3, LOW);

  //Set secondary projector to forward
  digitalWrite(proj_second_fwd_pin, HIGH);
  digitalWrite(proj_second_bwd_pin, LOW);
  digitalWrite(proj_second_pin, LOW);
  
}

void log (String msg) {
  if (debug_state) {
    Serial.println(msg);
  }
}

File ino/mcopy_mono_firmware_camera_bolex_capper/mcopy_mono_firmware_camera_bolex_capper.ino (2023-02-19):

/**
 * This is a specialized version of the mcopy firmware for
 * controlling the JK104-R/Bolex camera of the optical printer 
 * at MONO NO AWARE. This uses a Sainsmart 8 Solid State Relay 
 * board wired into the directional switches of a JK104-R/Bolex camera 
 * controller box, a secondary projector controller box and it 
 * runs on an Arduino Uno compatible board.
 * 
 * 7/17/2022
 * 
 * This firmware has been modified to include an optional capper element.
 * 
 * Pins 
 * 12 - CH1 - BWD CAM 1
 * 11 - CH2 - FWD CAM 1 (bridged to CH1)
 * 10 - CH3 - BWD CAM 1
 * 09 - CH4 - FWD CAM 1  (bridged to CH3)
 * 08 - CH5 - BWD CAM 1
 *  - controls the directional relays of the Bolex Camera.
 * 07 - CH8 - 4 pronged trigger cable
 *  - triggers the camera
 * 
 * 06 - SIGNAL - Capper servo signal
 * 05 - GND - Closed circuit to GND in cable to detect capper is attached.
 */

#include <Servo.h>

boolean debug_state = false;

Servo servo;

const int cam_bwd_pin_1 = 12;
const int cam_fwd_pin_1 = 11;
const int cam_bwd_pin_2 = 10;
const int cam_fwd_pin_2 = 9;
const int cam_bwd_pin_3 = 8;
const int cam_pin = 7;
const int capper_pin = 6; //servo
const int capper_exists_pin = 5;

const int cam_momentary = 60;
const int cam_time = 600; //secondary projector speed
const int cam_delay = 42;

volatile boolean cam_dir = true; 
volatile boolean cam_running = false;
volatile boolean capper_exists = false;
volatile boolean capper_state = false;

volatile int capper_angle = 0; 
const int capper_on_angle = 153; // tune this variable to your servo
const int capper_off_angle = 93; // -60 degrees apart

//SG-5010 speed 0.18s / 60 degree
//
//converted to milliseconds/angle
const float servo_speed = 400.0 / 60.0;

const char cmd_camera = 'c';
const char cmd_cam_forward = 'e';
const char cmd_cam_backward = 'f';

const char cmd_debug = 'd';
const char cmd_connect = 'i';
volatile char cmd_char = 'z';
const char cmd_mcopy_identifier = 'm';
const char cmd_cam_identifier = 'k';

const char cmd_camera_capper_identifier = '8';
const char cmd_capper_on = 'A';
const char cmd_capper_off = 'B';

const int serialDelay = 5;

void setup() {
  Serial.begin(57600);
  Serial.flush();
  Serial.setTimeout(serialDelay);
  
  pinMode(cam_fwd_pin_1, OUTPUT);
  pinMode(cam_bwd_pin_1, OUTPUT);
  
  pinMode(cam_fwd_pin_2, OUTPUT);
  pinMode(cam_bwd_pin_2, OUTPUT);
  
  pinMode(cam_bwd_pin_3, OUTPUT);
  
  pinMode(cam_pin, OUTPUT);

  pinMode(capper_exists_pin, INPUT_PULLUP);

  digitalWrite(cam_pin, LOW);
  
  digitalWrite(cam_fwd_pin_1, HIGH);
  digitalWrite(cam_fwd_pin_2, HIGH);
  
  digitalWrite(cam_bwd_pin_1, LOW);
  digitalWrite(cam_bwd_pin_2, LOW);
  digitalWrite(cam_bwd_pin_3, LOW);

  capper_init();
}

void loop() {
  if (Serial.available()) {
    /* read the most recent byte */
    cmd_char = (char)Serial.read();
  }
  if (cmd_char != 'z') {
    cmd(cmd_char);
    cmd_char = 'z';
  }
}

void cmd (char val) {
  if (val == cmd_debug) {
    debug();
  } else if (val == cmd_connect) {
    connect();
  } else if (val == cmd_mcopy_identifier) {
    identify();
  } else if (val == cmd_camera) {
    camera();
  } else if (val == cmd_cam_forward) {
    cam_direction(true);
  } else if (val == cmd_cam_backward) {
    cam_direction(false);
  } else if (capper_exists && val == cmd_capper_on) {
    capper_on(false, false);
  } else if (capper_exists && val == cmd_capper_off) {
    capper_off(false, false);
  }
}

void debug () {
  debug_state = true;
  Serial.println(cmd_debug);
  log("debugging enabled");
}

void connect () {
  Serial.println(cmd_connect);
  log("connect()");
}

void identify () {
  if (capper_exists) {
    Serial.println(cmd_camera_capper_identifier);
  } else {
    Serial.println(cmd_cam_identifier);
  }
  log("identify()");  
}

void camera () {
  if (!cam_running) {
    cam_running = true;
    digitalWrite(cam_pin, HIGH);
    
    delay(cam_momentary);
    digitalWrite(cam_pin, LOW);
  
    delay(cam_time - cam_momentary + cam_delay);
    
    Serial.println(cmd_camera);
    log("camera()");
    cam_running = false;
    
  }
}

void cam_direction (boolean state) {
  cam_dir = state;
  digitalWrite(cam_fwd_pin_1, LOW);
  digitalWrite(cam_fwd_pin_2, LOW);

  digitalWrite(cam_bwd_pin_1, LOW);
  digitalWrite(cam_bwd_pin_2, LOW);
  digitalWrite(cam_bwd_pin_3, LOW);

  if (state) {
    digitalWrite(cam_fwd_pin_1, HIGH);
    digitalWrite(cam_fwd_pin_2, HIGH);
    
    Serial.println(cmd_cam_forward);
    log("cam_direction -> true");
  } else {
    digitalWrite(cam_bwd_pin_1, HIGH);
    digitalWrite(cam_bwd_pin_2, HIGH);
    digitalWrite(cam_bwd_pin_3, HIGH);
    
    Serial.println(cmd_cam_backward);
    log("cam_direction -> false");
  }
  //delay(50); //delay after direction change to account for slippage of the belt
}

boolean does_capper_exist () {
  boolean exists = false;
  if (digitalRead(capper_exists_pin) == 0) {
    exists = true;
  }
  return exists;
}

void capper_init () {
  capper_exists = does_capper_exist();
  if (capper_exists) {
    log("Capper exists");
    servo.attach(capper_pin);
    capper_off(true, true);
  }
}

void set_capper_angle (int newAngle) {
  int delay_time = get_capper_delay(newAngle, capper_angle) + 50;
  servo.write(newAngle);
  delay(delay_time);
  capper_angle = newAngle;
}

int get_capper_delay (int angleA, int angleB) {
  int range = abs(angleA - angleB);
  return (int) ceil((float) range * servo_speed);
}

void capper_off (boolean suppress, boolean force) {
  int current_angle = servo.read();
  if (capper_state || current_angle != capper_off_angle) {
    set_capper_angle(capper_off_angle);
    capper_state = false;
  } else {
    log("Capper already off");
  }
  log("cap_off()");
  if (!suppress) {
    Serial.println(cmd_capper_off);
  }
}

void capper_on (boolean suppress, boolean force) {
  int current_angle = servo.read();
  if (!capper_state || current_angle != capper_on_angle) {
    set_capper_angle(capper_on_angle);
    capper_state = true;
  } else {
    log("Capper already on");
  }
  log("capper_on()");
  if (!suppress) {
    Serial.println(cmd_capper_on);
  }
}

void log (String msg) {
  if (debug_state) {
    Serial.println(msg);
  }
}

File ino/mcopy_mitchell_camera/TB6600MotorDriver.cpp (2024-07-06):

#include "TB6600MotorDriver.h"

TB6600MotorDriver::TB6600MotorDriver() {
	//
}

TB6600MotorDriver::TB6600MotorDriver(uint8_t enablePin, uint8_t directionPin, uint8_t pulsePin, uint32_t usPulse, uint8_t microsteps) {
	_enablePin = enablePin;
	_directionPin = directionPin;
	_pulsePin = pulsePin;

	_usPulse = usPulse;
	_microsteps = microsteps;
	_revsteps = 200 * microsteps;
}


void TB6600MotorDriver::setup() {
	if (_enablePin != 0) {
		pinMode(_enablePin, OUTPUT);
	}
	pinMode(_directionPin, OUTPUT);
	pinMode(_pulsePin, OUTPUT);

	digitalWrite(_directionPin, LOW);
	digitalWrite(_enablePin, _enabled ? HIGH : LOW);
}

void TB6600MotorDriver::setDirection(bool direction) {
	if (direction != _direction) {
		_direction = direction;
		_setDirection();
	}
}

void TB6600MotorDriver::_setDirection () {
	digitalWrite(_directionPin, _direction ? LOW : HIGH);
}

void TB6600MotorDriver::setSpeed(uint16_t rpm) {
	_usPulse = 60000000 / ((uint32_t) _revsteps * (uint32_t) rpm);
}

void TB6600MotorDriver::steps(uint64_t stepCount) {
	for (uint64_t i = 0; i < stepCount; i++) {
		_step();
	}
}

void TB6600MotorDriver::_step() {
	digitalWrite(_pulsePin, HIGH);
	delayMicroseconds(_usPulse);
	digitalWrite(_pulsePin, LOW);
	delayMicroseconds(_usPulse);
}

void TB6600MotorDriver::step() {
	_step();
}

void TB6600MotorDriver::release() {
	_enabled = false;
	_setEnable();
}

void TB6600MotorDriver::enable() {
	_enabled = true;
	_setEnable();
}

void TB6600MotorDriver::_setEnable() {
	if (_enablePin != 0) {
		digitalWrite(_enablePin, _enabled ? HIGH : LOW);
	}
}

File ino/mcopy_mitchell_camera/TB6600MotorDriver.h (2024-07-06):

#ifndef TB6600MotorDriver_h
#define TB6600MotorDriver_h

#include <Arduino.h>

/**
 * Default pins
 * D6 Enable +
 * D7 Direction +
 * D8 Pulse +
 **/

class TB6600MotorDriver {
  private:

  volatile uint8_t _enablePin = 0; //0 is disabled
  volatile uint8_t _directionPin = 7;
  volatile uint8_t _pulsePin = 8;

  volatile uint32_t _usPulse = 300;

  //physically set, can't change
  volatile uint8_t _microsteps = 1;   //1, 2, 4, 8, 16, 32

  volatile uint16_t _revsteps = 200; // # steps per revolution
  volatile bool _direction = true;
  volatile bool _enabled = true;

  void _step();
  void _setDirection();
  void _setEnable();

  public:

  TB6600MotorDriver();
  TB6600MotorDriver(uint8_t enablePin, uint8_t directionPin, uint8_t pulsePin, uint32_t usPulse, uint8_t microsteps);

  void setup();

  void setDirection(bool direction);
  void setSpeed(uint16_t rpm);

  //full
  void steps(uint64_t stepCount);
  void step();

  void enable();
  void release();
};

#endif

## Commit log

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2016-04-11 Fix model, Pixie only uses rgb
    [mcopy_light.ino]
2016-04-11 Lighting testbed using pixels instead of pixies
    Neopixels are sub-watt and pixies are 3W, this will prevent major eye
    damage when testing lighting firmware
    [mcopy_light_tests.ino]
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2016-04-22 Correctly manage memory when reading from endstop
    [mcopy_projector_tests.ino]
2016-05-04 Add arduino mount and pins libraries
    These will be used in the mcopy hardware designs
    [arduino.scad, pins.scad]
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2016-05-09 Flip raw reading logic for microswitch
    Using a microswitch with INPUT_PULLUP instead of an endstop. As a
    result 1 == switch closed instead of 0 == endstop closed.
    [mcopy_projector_tests.ino]
2016-05-13 Update test and firmware files to update Pixie every sec
    Send a signal to change the color of the light every second to prevent
    them from getting “stuck” re:
    https://learn.adafruit.com/pixie-3-watt-smart-chainable-led-pixels/
    “You do have to send it data every 1 second at a minimum (as a
    protection against the bright and hot LEDs staying 'stuck on', they
    will eventually timeout if no updates are received)”
    [mcopy_light.ino, mcopy_light_tests.ino]
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2016-06-19 Compilation of app.js after push to modules
    It’s, like, 100 lines shorter!
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2017-12-28 V1 of the jk connector, split into 2 parts to be assembled and attached.
    [common.scad, connectors.scad]
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2017-12-29 Include development work from previous projects. Create an "mcopy.scad" file for laying out all parts in a single space (for renders).
    [light.scad, mcopy.scad, motor.scad]
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2017-12-31 Add prism module to potentially use [this prism](http://amzn.to/2ChhcNy) in the design of a light with 3 [Adafruit Pixies](https://www.adafruit.com/product/2741), 9W at max. Potentially a stupid idea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
    [light.scad]
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2018-01-02 All work to date on hardware. Made connectors, started carriage and re-started light.
    [carriage.scad, light.scad, mcopy.scad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]
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2018-01-02 Distinguish devices with an empty array if there's an error listing devices OR if there are none found.
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2018-01-16 The light is ready to print with an arbitrary stand for the bell and howell projector.
    [mcopy.scad, motor.scad]
2018-01-16 Add the experimental "fresnel" pattern generator for laser cutting. The hypothesis is that by melting the surface of an acrylic sheet, light from the LED source will be better projected forward onto 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
    [light.scad, mcopy.scad, motor.scad]
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2018-01-18 The arbitrary mount allows the diffuser mount to slide along a horizontal axis.
    [light.scad, mcopy.scad]
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2018-02-01 Fix the command button states, spacing and icon placement
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2018-03-15 To preserve the light functionality, the light command needed to have its await statements re-organized. Issue was that light values issued to the firmware take the form of sending the character "l" 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
2018-03-15 Minor version increment, 1.0.0 was broken, and this is a corrective patch. 1.0.1 allows connected light devices to work without locking up the process.
2018-03-15 Improve linux build process. Caught an issue where the binary mcopy is conflicting with another in the mtools library. Will be re-naming the binary mcopy-app on linux. Will revist this after current 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
2018-07-03 Momentary switch delay was too long.
    [mcopy_jk_firmware.ino]
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2019-02-09 Reverse High/low for relay
    [mcopy_camera_relay.ino]
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2019-02-11 Fix loop bug. When selection a video as a projector (need to work on this metaphor) the loops are automatically set. Previous issues were due to id re-use.
    Also, (almost) you can choose a light color value that a frame will be overlayed on with a Darken composite mode. This is almost working but is kludgey because the first frame is always coming up black. Will need to make adjustments in the light module.
2019-02-13 Okay. Removed the light.state.on behavior. Now, a frame is rendered to the set color state of the "light" only when the camera is moving. Unnecessary frames don't display AND the correct color is rep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
2019-02-26 Fix projector_second component code.
    [mcopy_projector_second.ino]
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2019-03-18 Add ANYEYE scad work. Contains the motor key for connecting the INTVAL2/3 style motor mount and microswitch to a Revere 16mm projector.
    [anyeye_revere.scad]
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2019-03-18 Create a scad file for extra odds and ends for the JK
    [jk_extras.scad]
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2019-03-21 Add correct alias strings to arduino lib
2019-03-21 Remove console logging from arduino lib. Reject or throw to log errors
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2019-03-21 Remove dev object and replace with new devices module. Log an error on failure to enumerate devices that isn't caught within the method.
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2019-03-21 Print state for now. Need to store position in it? Make resetting it simple.
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2019-03-22 Took a tiny detour on the film out feature, or "digital projector". This now avoids showing a browser window fullscreen on mac, which is having performance issues when opening and then running sequen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
2019-05-28 Wire goto button on projector 2 and camera 2 to cmd.projector_second_to and cmd.camera_second_to. Resolves #9
2019-05-28 Refactored seq.js to Typescript and fixed stats for 1 cam 1 proj. Will need further work to add in multiple devices. Resolves #6.
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2019-06-25 Fixed frame counting optimization, resolving issue #17. Also added a Siemens Star focusing screen, a middle gray metering screen and a field guide screen for use with the filmout feature. TODO: actua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
2019-07-25 Incorrectly bound counter to wrong device.
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2019-08-04 App was throwing error during filmout. Re-wrote the resizing logic so that if it can't find dimensions in the info, don't resize the image. This may lead to squashing, as I've seen in frameloom, but 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
2019-08-15 Properly count number of frames in animated gifs using `identify` from imagemagick because ffprobe was failing.
2019-08-25 If filmout picture source is set, set the field guide to match the aspect ratio of the image. Right now that only works if ratio is lower than the screen. Need to add case in display.html that correc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
2019-10-04 Sequencer now blocks system sleep while running a sequence. Made me upset last night when it happened during a filmout and I shot 1000 frames of black. Resolves #26
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2020-01-09 Resolves #34. Added delay lib to renderer and added a magic delay before ending devices.ready(). Just works. Move on and don't question it.
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2020-02-21 Pre-export all frames in video (with confirmation dialog). Greatly improves sequence times and reliablity in conjunction with last commit. Resolves #36 and resolves #39.
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2020-07-27 Fixed serialization error that was breaking raspberry pi 4 installation. It is apparently a real bug that should be breaking the app.
2020-07-27 Squash errors in case of mkdir trying to create an existing directory (need mkdirp, but this works without an extra module)
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2020-08-10 Log doesn't need to print its own path.
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2020-09-29 Fixed typo in Pins() where PROJECTOR_FWD was set to LOW twice instead of PROJECTOR_BWD.
    [mcopy_JKMM99.ino]
2020-09-29 Re-write of the JKMM99 which replaces the relay-based camera controller with an intval-based one. This relies on the Arduino Uno in the control box to handle all of the control logic in place of an o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
    [mcopy_JKMM99_intval.ino]
2020-09-29 Work towards issue #52. Adds a statement within the arduino.end() method that watches for an 'E' char byte and will alert the UI while pausing a running sequence. Needs to be in place for firmware to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
2020-09-29 Addressing the issue with the JKMM99 projector functionality where frames stop prematurely. Conceivably, the proj_microswitch() function is the only place that calls proj_stop() so the issue is with 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
    [mcopy_JKMM99.ino]
2020-09-29 Edit addresses the issue implied by #52. In simple tests with improvised hardware, frame cannot complete in less than 450ms, which is half a full frame. Will add another check to proj_stop() to evalu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
    [mcopy_JKMM99.ino, mcopy_JKMM99_intval.ino]
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2021-02-24 Corrected an issue with the monitor selection UI where the text is cut off.
2021-02-24 Added an edge-case helper for choosing files/directories in linux. This finishes the requirement for issue #50 on linux, but will test changes on macOS before marking the issue resolved.
2021-03-18 Filmout needs to receive the whole state, not just the frame. Still broken.
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2022-06-07 Hardware ideas for capper mount and flag. Need to model servo and add places for endstops
    [capper.scad, common.scad]
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2022-06-12 All capper work. Debug firmware for testing. STL of cap as printed.
    [capper.scad, capper_cap.stl]
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2022-06-16 Work on the opto endstop mount. This needs to be re-oriented before next print.
    [capper.scad, capper_opto_endstop_mount.stl]
2022-06-18 More mount work and start of endstop logic. Rebuilding the B&H projector unity.
    [capper.scad, jk_projector_knob.stl]
2022-06-20 Updates to endstop mount design. Had incorrectly positioned voids for SMD chips on the endstop
    [capper.scad, capper_opto_endstop_mount.stl]
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2022-06-28 Reduce the size of the void for the screw in the cap.
    [capper.scad]
2022-06-28 Re-render all STLs for capper, removing the opto endstop component (for now)
    [capper_cap.stl, capper_mount_back.stl, capper_mount_front.stl]
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2022-07-13 All capper work. Need to wrap all actions in the 'b' command and push functionality to a lower level to prevent unneeded complexity.
    [capper.scad]
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2022-07-17 Fix debug script and component
    [mcopy_capper.ino, mcopy_servo_debug.ino]
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2022-08-07 Caught a possible ancient bug in the loop logic for calculating state of camera and projector backwards movements.
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2022-10-19 DC motor design has all components designed, need to print, test and adjust.
    [arri_s.scad, takeup.scad]
2022-10-21 Add set screw for bearing and counter sink bolt caps for other cap m3s
    [arri_s.scad]
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2022-10-28 Pausing work on arri_s_DC firmware because hardware is less than ideal. Too much play in the motor position to trust right now. Steppers better approach.
    [mcopy_arri_s_DC_firmware.ino]
2022-10-28 Work on stepper motor design and software. Motor still moves more slowly than it should but will investigate multiple factors leading to this result
    [arri_s.scad]
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2022-11-04 Stepper firmware is working. Needed extra tape around coupling connector to add friction to connection and now it keeps.
    [arri_s.scad]
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2023-01-02 Increase the inner diameter of the bellows board to allow the threads to pass through cleanly and be held in place by the screw
    [bellows.scad]
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2023-01-02 Adjust the height of the mount (-14.5mm) and make bolt voids larger
    [arri_s_mount.scad]
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2023-01-04 All arri s mount and jk lens assembly work. need to do some branch cleanup on this project and tackle capper issues for merge of this branch.
    [arri_s_camera_bellows_board.stl, arri_s_mount.scad, arri_s_mount.stl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]
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2023-01-14 Adjust the position of the Z axis, move the linear bearing up and down to prevent binding on motion
    [jk_lens_assembly.scad]
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2023-02-25 Adding contextIsolation: false to the display module fixes the initial issue in #74, cannot use "require" but the escape button does not work due to "Cannot read properties of undefined (reading 'get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
2023-02-26 Add work on mcopy_cam_canon. This includes teh CanonBLERemote library, ArduinoNvs (dependency of CanonBLERemote) and TickTwo, potentially to manage a blinking UI component. Not working. Finish the fi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
    [CanonBLERemote.cpp]
2023-02-28 Timing is now updated via rolling average on all projector and camera actions. This data is reset when profile is changed. This data is stored in the settings.json and loaded on start so estimates wi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
2023-03-01 Improve timing. Sequence takes into account serialDelay within each command and sequenceDelay has no bearing. Was adding 120ms of error to every step
2023-03-05 Add common SCAD lib. Add a script that compiles all scad files to stl (make is getting excessive). Canonicalize STL files after they're compiled.
    [mcopy_mono99_electronics_mount.stl, projector_controller.scad]
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2023-03-18 Use the correct pins for the projector
    [mcopy_JKMM100.ino]
2023-03-20 Work in progress: Serial does not work from external library
    [jk.scad, mcopy_projector.scad]
2023-03-22 Fixed issue with baud being stored as const overflowed. Silly mistake.
    Also storing command chars as public const variables to shorten code and allow for mc.COMMAND rather than McopySerial::COMMAND. Cleans up example code a lot.
    [McopySerial.cpp, McopySerial.h, mcopy_JKMM100.ino]
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2023-03-26 Adjust angles. Make $fn configurable (crashing the GUI on my desktop).
    [cpc_connectors.scad]
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2023-04-12 Correctly reference LEDs
    [bellows.scad]
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2023-04-12 Correctly delay between frames.
    [mcopy_cam_canon_ble.ino]
2023-04-12 Correctly reference backward LED
    [mcopy_JKMM100.ino]
2023-04-12 Relay logic was reversed
    [mcopy_cam_relay.ino]
2023-04-14 Invert logic for use with solid state relays rather than standard
    [mcopy_JKMM100.ino]
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2023-04-17 Add a bellows board -- to be attached to bellows and then to boards with magnets. Render all STLs
    [bellows.scad, bellows_board_magnetic.stl, bellows_camera_board.stl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]
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2023-05-15 Create first draft of projector panel redesign
    [mcopy_projector.scad]
2023-05-15 Flip projector panel to print
    [mcopy_projector.scad]
2023-05-15 Bearing needs slight gap to allow the inner bearing wheel to rotate freely
    [mcopy_projector.scad]
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2023-06-29 fix reference to cmdChar
    [mcopy_cam_canon_ble.ino]
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2023-07-04 Use the correct identifier on projectors
    [mcopy_mono_firmware_projectors.ino]
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2023-07-04 Add missing lines to debug sketch
    [mcopy_projector_debug.ino]
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2023-08-20 All work towards creating a sled rail for the lens carriage assembly
    [rails_2020.scad]
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2023-08-21 Update part names of bellows.scad. Render missing magnetic board.
    [bellows.scad, bellows_lens_board_magnetic.stl]
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2023-08-22 Run on all but 1 core. Update JK rails to use actual measurement
    [jk_rails.scad]
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2023-08-24 Add structures to insert 2020 Tslot into to make rails fit more snug
    [mcopy_rails.scad, mcopy_rails_lens_sled.stl, mcopy_rails_rail_end.stl]
2023-08-25 Work on projector: Still having issues with IteadDualStepperShield (addresses wrong motor, wrong number of steps).
    [McopyProjector.cpp, McopyProjector.h]
2023-08-29 Rewrite mcopy_projector_firmware with AccelStepper, replacing the custom Itead firmware (not working)
    [McopyProjector.cpp, McopyProjector.h, mcopy_projector_firmware.ino]
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2023-09-04 Add additional bearings to lens sled and voids for m5 bolts to hold in side bearings.
    [mcopy_rails.scad, mcopy_rails_rail_end.stl, mcopy_rails_rail_end_idle.stl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]
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2023-09-06 Remove part of the 2020 ends so that it can print without supports
    [mcopy_rails.scad]
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2023-09-15 Work on projector (wrong)
    [mcopy_projector.scad, mcopy_projector_gate_key.stl]
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2023-09-25 Create the first design of the orbital mount and make slight adjustment to panel (screws were not attaching fully).
    [mcopy_projector.scad]
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2023-09-26 Projector firmware progress: currently the homing function will not compile due to errors with reference and so the sketch method needs to be broken into workable smaller methods
    [McopyProjector.cpp, McopyProjector.h, mcopy_projector_firmware.ino]
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2023-09-29 Disable home feature for now. Fixed impossibly stupid bug with reverse mode. Used uint16_t rather than int16_t causing an overflow.
    [McopyProjector.cpp, mcopy_projector_firmware.ino]
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2023-10-06 Update rack and pinion library to one that produces valid geometry. Make first pass at rack and pinion gear
    [mcopy_projector.scad, rack_and_pinion.scad]
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2023-10-08 Update servo gear to fit reinforced servo connectors.
    [mcopy_projector.scad]
2023-10-08 Fix for case where this.confirmExec is not a function
2023-10-09 Tweak to the rack and pinion mechanism to allow it to fit.
    [mcopy_projector.scad]
2023-10-09 Add BOM log lines and move rail ends into its own module
    [mcopy_rails.scad]
2023-10-09 Add servo functionality for rack and pinion motion. Need to fix home feature.
    [McopyProjector.cpp, McopyProjector.h, mcopy_projector_firmware.ino]
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2023-10-09 Caught one bug after separating out code
    [McopyProjector.cpp]
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2023-10-10 Add more smoothing during homing step. Is running consistently but is ending with motor in wrong position each time. Very strange.
    [mcopy_projector_firmware.ino, mcopy_projector_homing_debug.ino]
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2023-10-31 Work on rails and lens gantry. First prototype is made. Rendering all.
    [jk_lens_assembly.scad, mcopy_lens_assembly.scad, mcopy_rails.scad]
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2023-11-26 Developed a seemingly working fix with the "correction loop" strategy. Might be putting the motor through hell but it is consistent.
    [mcopy_JKMM100_work.ino]
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2023-12-01 Fix plug diameter
    [cpc_connectors.scad]
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2023-12-01 Fix the dual projector script and add notes
    [mcopy_mono_firmware_projectors.ino]
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2023-12-28 Fix bolt countersink in bolex mounting block. Add center line to top
    [mcopy_rails.scad]
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2024-04-07 List of devices looks strange on laptop. Attempt at fix here
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2024-04-15 Correctly reference common.scad and add file for camera mount.
    [canon_rf_ACME_bellows_adapter.scad, canon_rf_ACME_camera_mount.scad]
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2024-05-19 In a two device simultaneous action, the cmd module was attemptint to await both actions in an array. This was not working and caused await to not occur. Instead, all actions have been replaced by a 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
2024-05-23 Update Settings class to export properly. Replace use of any in Device.
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2024-05-24 Do not display broken layout before devices are ready
2024-05-24 Updated tests to add cases catching mscript failing on multi-device scripts
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2024-06-30 Fix ino.sh script. Add pin declarations to EndstopCameraShield
    [EndstopCameraShield.cpp, EndstopCameraShield.h, mcopy_oxberry_camera.ino]
2024-06-30 Accidentally modified an autogenerated part of McopySerial. Fixed
    [EndstopCameraShield.cpp, EndstopCameraShield.h, McopySerial.h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]
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2024-08-03 Add getDirection() to EndstopCameraShield and fix sloppy bugs in code that were not disabling emitters after actions. Could have caused false positives in behavior so check on the machine
    [EndstopCameraShield.cpp, EndstopCameraShield.h]
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2024-09-13 Save gate work (broken).
    [mcopy_gate.scad]
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2024-09-14 Fix text labels on gates
    [mcopy_gate.scad]
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2024-10-13 Fixed single issue related to #11. If state of secondary projector or camera are set, include in output.
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2024-10-23 Replace all bolts in m3 with m2.5 bolts.
    [mcopy_gate.scad, mcopy_gate_back_plate.stl, mcopy_gate_body_16mm.stl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]
2024-10-25 Work on gate, need to add catch to slide to prevent from coming out too far with spring-loaded action
    [mcopy_gate.scad]
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2024-11-09 Work on adding reinforcement to the electronics mount.
    [projector_controller.scad]
2024-11-13 Work on mcopy gate. Adjustments to plate sizes (made front_plate thicker to print better without cracking)
    [mcopy_gate.scad, mcopy_gate_back_plate.stl, mcopy_gate_front_plate.stl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]
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2026-02-13 Working through bugs in mitchell code
    [mcopy_mitchell_camera.ino, mcopy_oxberry_camera.ino]
2026-02-16 Fixed issue with mitchell and oxberry scripts. Double exposure and long exposure issues were logic-based bugs and EndstopCameraShield has been modified to be more explicit about camera position when 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
    [EndstopCameraShield.cpp, mcopy_mitchell_camera.ino, mcopy_oxberry_camera.ino]
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
